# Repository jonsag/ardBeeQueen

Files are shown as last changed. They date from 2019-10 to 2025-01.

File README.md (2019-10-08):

# ardBeeQueen
A simple project to control a bee queen breeding chamber

Parts needed
===============
1 x Arduino Pro Mini, kjell.com art#87964  
1 x Arduino USB to Serial Converter, kjell.com art#87872  
2 x Arduino Single Relay Module, kjell.com art#87878  
1 x LCD Display, kjell.com art#90215  
1 x Dallas 1-wire Temp and Humidity Sensor DHT11, kjell.com art#87877 or  
1 x Dallas 1-wire Temp and Humidity Sensor DHT22, kjell.com art#90647  
1 x Rotary encoder, kjell.com art#87918  
1 x 10kohm Potentiometer, kjell.com art#90633  
1 x 220ohm resistor  
1 x 10K ohm resistor  
2 x 0,47uF capacitor  

Casing to hold everything

Wires and soldering material  

If you want to build a PCB using the Gerber file you will also need some headers and connnectors.  

Building electrical  
===============
Use schemes ardBeeQueenFritz* or Schematic_ardBeeQueen-v2_ardBeeQueen-v2_* to build.  
If you do not use the encoder you must still pull up D7 with a 10K resistor to VCC.  

Eagle PCB  
===============
If using the 50x52 PCB in Documents/Eagle directory, you can mount it in box electrokit.com, art#12109003  
Outside measures: 69 x 102 x 37 mm  
Inside measures: 63 x 96 x 33 mm  

If using the 105x84 PCB in Documents/Eagle directory, you can mount it in box electrokit.com, art#12109005  
Outside measures: 103 x 148 x 56 mm  
Insode measures: 96 x 142 x 52 mm  

Note
===============
All commands in the following instructions are run on Linux  
All links are valid and versions are the latest as of february 2019  

Set up Arduino IDE
===============
Go to https://www.arduino.cc/en/main/software and download Arduino IDE for your architecture and system  
>$ wget https://downloads.arduino.cc/arduino-1.8.10-linux64.tar.xz  
>$ tar xvJf arduino-1.8.10-linux64.tar.xz -C ~/bin/  
>$ ln -s arduino-1.8.10/arduino ~/bin/arduino  

Get libraries 
---------------

Adafruit Unified Sensor library  
---------------
Download library from https://www.arduinolibraries.info/libraries/adafruit-unified-sensor  
>$ wget http://downloads.arduino.cc/libraries/github.com/adafruit/Adafruit_Unified_Sensor-1.0.3.zip  
>$ unzip Adafruit_Unified_Sensor-1.0.3.zip -d ~/bin/arduino-1.8.10/libraries/  
>$ mv ~/bin/arduino-1.8.10/libraries/Adafruit_Unified_Sensor-1.0.3 ~/bin/arduino-1.8.10/libraries/Adafruit_Unified_Sensor  

DHT sensor library  
---------------
Download library from https://www.arduinolibraries.info/libraries/dht-sensor-library  
>$ wget http://downloads.arduino.cc/libraries/github.com/adafruit/DHT_sensor_library-1.3.7.zip  
>$ unzip DHT_sensor_library-1.3.7.zip -d ~/bin/arduino-1.8.10/libraries/  
>$ mv ~/bin/arduino-1.8.10/libraries/DHT_sensor_library-1.3.7 ~/bin/arduino-1.8.10/libraries/DHT_sensor_library  

Programming the Arduino Mini Pro
===============

If using the Arduino USB 2 Serial  
--------------------
Connect the programmer to your Pro Mini  
GND/BLK -> GND  
+5V -> VCC  
TX -> RX  
RX -> TX  
EXT RESET -> GRN

Open your sketch in Arduino IDE  
Select 'Tools'->'Port'  
* /dev/ttyACM0 or  
* /dev/ttyUSB0  

Select 'Tools'->'Board'  
For the 3.3V versions of the Arduino Pro Mini, select:  
* Arduino Pro or  
* Pro Mini (3.3V, 8 MHz) w/ ATmega328P or  
* Arduino Pro or  
* Pro Mini (3.3V, 8 MHz) w/ ATmega168  
(depending on the microcontroller on your board)  
For the 5V versions of the Arduino Pro Mini, select  
* Arduino Duemilanove or  
* Nano w/ ATmega328P or  
* Arduino Diecimila, Duemilanove (this is what I used) or  
* Nano w/ ATmega168

If using the PC-PL2303 Cable  
---------------
Black cable -> GND  
Green cable -> TXD  
White cable -> RXD  
Red cable -> VCC (5V)  

You will have to press the reset button on the arduino to reset it right before the upload from Arduino IDE.  

Fritzing  
===============
Download fritzing at http://fritzing.org/download/  

>$ wget http://fritzing.org/download/0.9.3b/linux-64bit/fritzing-0.9.3b.linux.AMD64.tar.bz2  
>$ tar jxvf ~/Downloads/fritzing-0.9.3b.linux.AMD64.tar.bz2 -C ~/bin/  
>$ ln -s fritzing-0.9.3b.linux.AMD64/Fritzing ~/bin/fritzing  

EasyEDA  
==============
Use easyEDA online at https://easyeda.com/editor or download client from https://easyeda.com/page/download  

>$ wget https://image.easyeda.com/files/easyeda-client-linux-x64.zip  
>$ unzip easyeda-client-linux-x64.zip  
>$ cd easyeda-client-linux-x64  
>$ sudo bash install.sh  

Download local router from https://docs.easyeda.com/en/PCB/Route/index.html#Local-Auto-Router  
>$ wget https://image.easyeda.com/files/EasyEDA-Router-v0.8.1.zip  
>$ unzip EasyEDA-Router-v0.8.1.zip  
>$ cd EasyEDA-Router-v0.8.1  

Start router with  
>$ bash lin64.sh  

Autodesk EAGLE
===================
Download EAGLE at https://www.autodesk.com/products/eagle/free-download  

>$ tar xvzf Autodesk_EAGLE_9.3.1_English_Linux_64bit.tar.gz -C ~/bin  
>$ ln -s eagle-9.3.1/eagle ~/bin/eagle  

Start and sign in with your Autodesk account

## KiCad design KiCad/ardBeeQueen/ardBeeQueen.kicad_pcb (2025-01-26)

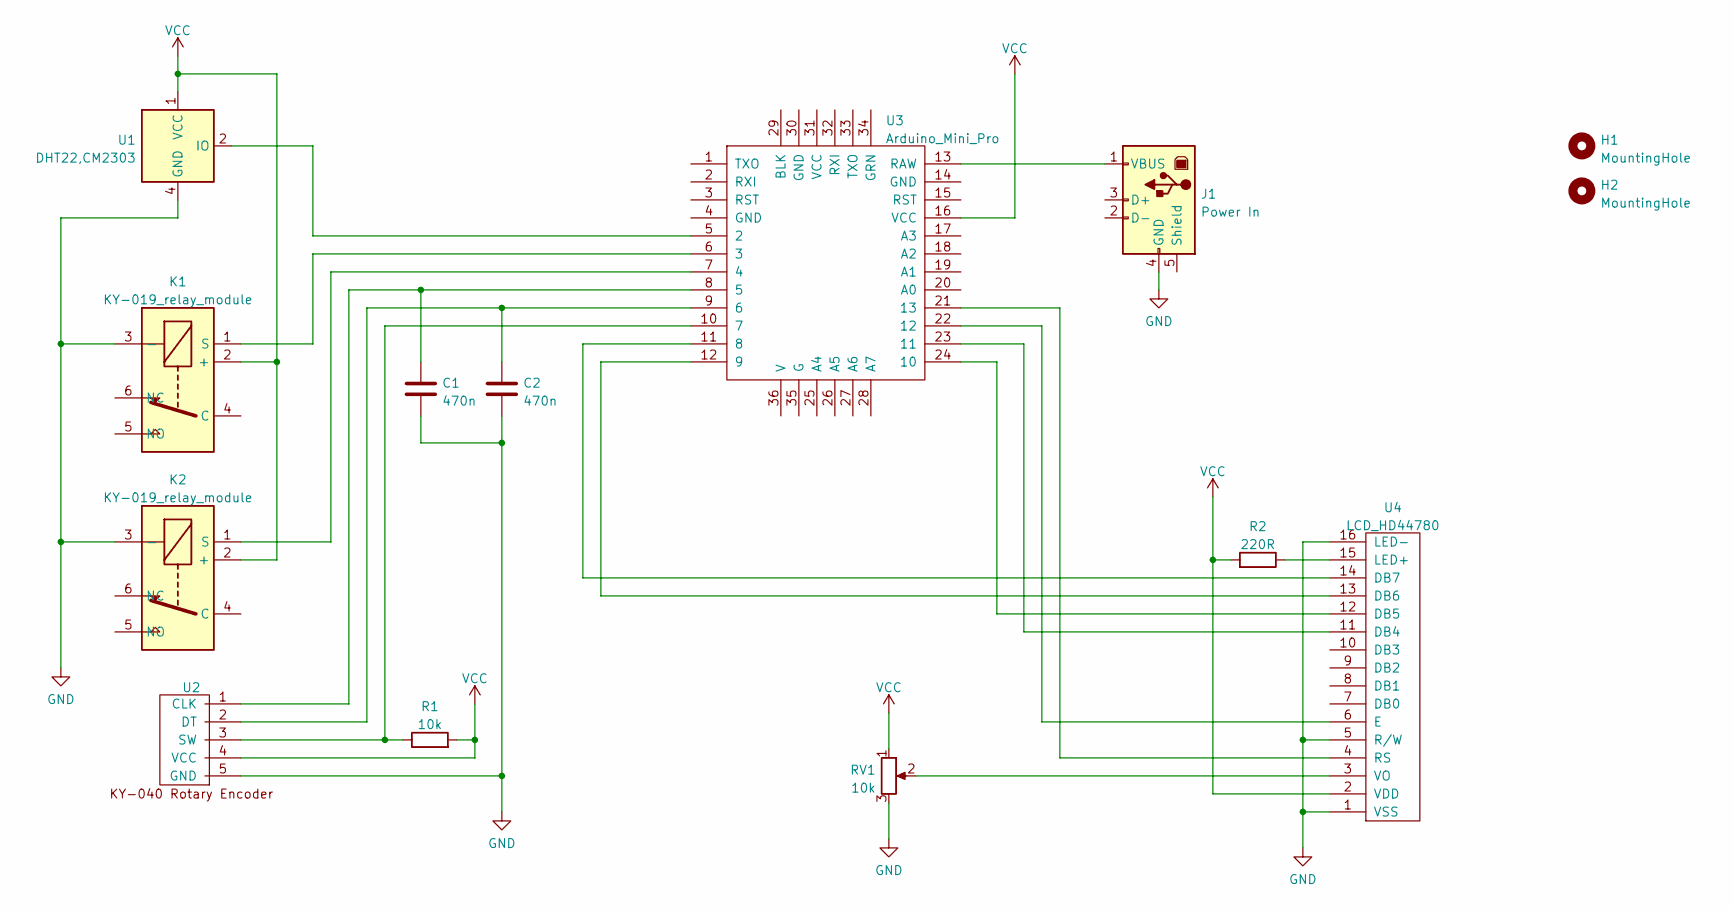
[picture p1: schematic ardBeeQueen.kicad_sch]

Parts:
C1, C2: 470n; C_Disc_D3.0mm_W1.6mm_P2.50mm_larg
H1, H2: MountingHole; MountingHole_3.2mm_M3
J1: Power In; USB_B_OST_USB-B1HSxx_Horizontal_large
K1, K2: KY-019_relay_module; 3-pin JST KY-019 relay
R1: 10k; R_Axial_DIN0207_L6.3mm_D2.5mm_P10.16mm_Horizontal_larger_pa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
R2: 220R; R_Axial_DIN0207_L6.3mm_D2.5mm_P10.16mm_Horizontal_larger_pa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
RV1: 10k; Potentiometer_Bourns_3339P_Vertical_large
U1: DHT22,CM2303; 3-pin JST DHT11, DHT22
U2: KY-040_Rotary_Encoder; 5-pin JST Rotary Encoder
U3: Arduino_Mini_Pro; Arduino_Pro_Mini_vC_only_sides_larger_pads
U4: LCD_HD44780; LCD_HD44780_16x2_w_headers_no outlinelarge

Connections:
GND: C1.2, C2.2, J1.4 (GND), K1.3 (-), K2.3 (-), RV1.3, U1.4 (GND), U2.5 (GND), U4.1 (VSS), U4.5 (R/W), U4.16 (LED-)
unnamed: C1.1, U2.1 (CLK), U3.8 (5)
unnamed: C2.1, U2.2 (DT), U3.9 (6)
unnamed: J1.1 (VBUS), U3.13 (RAW)
unnamed: K1.1 (S), U3.6 (3)
unnamed: K2.1 (S), U3.7 (4)
unnamed: R1.1, U2.3 (SW), U3.10 (7)
unnamed: R2.1, U4.15 (LED+)
unnamed: RV1.2, U4.3 (VO)
unnamed: U1.2 (IO), U3.5 (2)
unnamed: U3.11 (8), U4.14 (DB7)
unnamed: U3.12 (9), U4.13 (DB6)
unnamed: U3.21 (13), U4.4 (RS)
unnamed: U3.22 (12), U4.6 (E)
unnamed: U3.23 (11), U4.11 (DB4)
unnamed: U3.24 (10), U4.12 (DB5)
VCC: K1.2 (+), K2.2 (+), R1.2, R2.2, RV1.1, U1.1 (VCC), U2.4 (VCC), U3.16 (VCC), U4.2 (VDD)

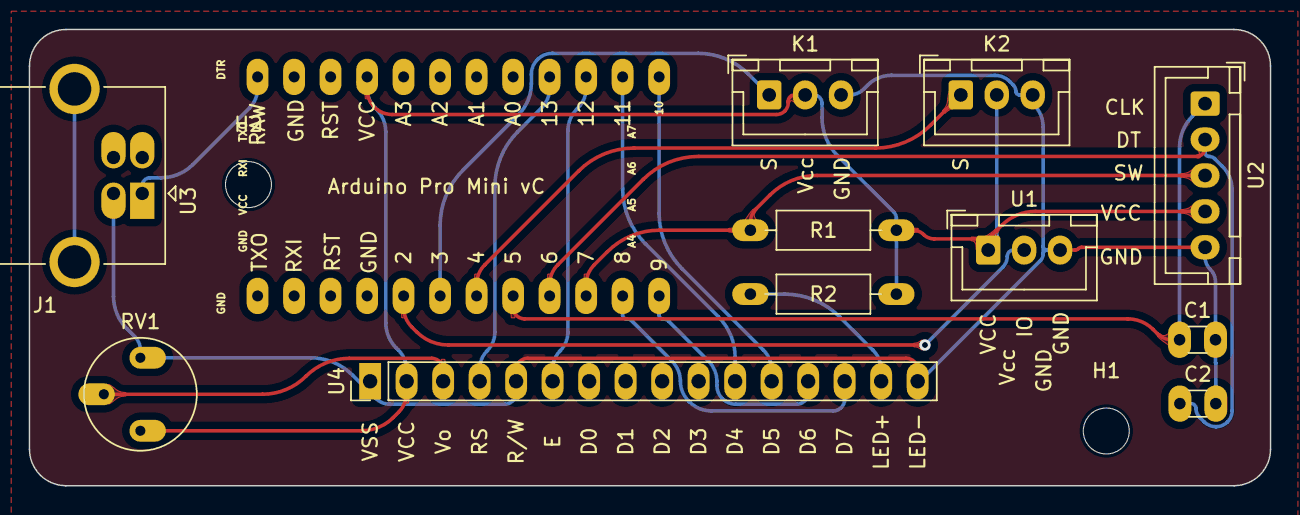
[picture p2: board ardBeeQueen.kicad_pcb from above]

Board: 2 copper layers, 86.4 x 31.7 mm, 14 parts (0 on the bottom side), 17 nets.

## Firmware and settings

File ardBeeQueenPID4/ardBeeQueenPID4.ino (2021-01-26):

String programName = "ardBeeQueenPID4";
String date = "201910020";
String author = "Jon Sagebrand";
String email = "jonsagebrand@gmail.com";

const bool plot = 1; // enable plotting function, all other output to serial will be suppressed

/*******************************
   EEPROM setup
 *******************************/
#include <EEPROM.h> // include EEPROM library
const int eeAddr = 0; // address to store the set point temp
double f; // stores the temp set in eeprom

/*******************************
   DHT setup
 *******************************/
#include <DHT.h> // include the DHT library
#define DHTPIN 2  // declare DHT pin number

// uncomment one of the below sensors
//#define DHTTYPE DHT11   // DHT 11 used
#define DHTTYPE DHT22   // DHT 22  (AM2302), AM2321
//#define DHTTYPE DHT21   // DHT 21 (AM230)

DHT dht(DHTPIN, DHTTYPE);  // initialize DHT sensor

unsigned long readMillis; // stores millis
const int waitTime = 2000; // millis to wait between reads

double hum = 0; // stores humidity
double temp = 0; // stores temperature
double dewPoint = 0; // calculated dew point
double dewPointFast = 0; // another calculated dew point
double hic = 0;

/*******************************
   Input/Output pins setup
 *******************************/
const int heatRelay = 3;  // heating relay
bool heatRelayState;
bool heatRelayStateLast = 0; // last state of operation

const int fanRelay = 4;  // cooling relay
bool fanRelayState = 0; // fan is always on/off
bool fanRelayStateLast = 0; // last state of operation

const int encoderCLK = 5; // rotary encoder CLK signal input pin
const int encoderDT = 6; // rotary encoder DT signal input pin
const int encoderSW = 7; // rotary encoders switch input pin, goes LOW when pressed

bool encoderCLKState = 0; // for storing encoder values
bool encoderDTState = 0;
bool encoderSWState = 0;
bool encoderDTStateLast = 0;
bool encoderSWStateLast = 0;

unsigned long encoderSWTimeMillis = 0; // the last time encoder button was toggled
const int debounce = 200;   // the debounce time, increase if the output flickers

/*******************************
   LCD setup
 *******************************/
#include <LiquidCrystal.h> // include the LCD library

// define LCD pins
const int LCD_RS = 13; // LCD RS, pin 4
const int LCD_EN = 12; // LCD E, pin 6, Enable
const int LCD_D4 = 11; // LCD D4, pin 11, databit 4
const int LCD_D5 = 10; // LCD D5, pin 12, databit 5
const int LCD_D6 = 9; // LCD D6, pin 13, databit 6
const int LCD_D7 = 8; // LCD D7, pin 14, databit7
/* other pins on LCD are:
   VSS, pin 1, GND
   VDD, pin 2, +5V
   V0, pin 3, 10k potentiometer, ends to +5V and GND, middle pin to V0, contrast
   R/W, pin 5, GND, Read/Write
   A, pin 15, 220ohm resistor, one end to +5V, other to A, back light anode, ~+4.2V
   K, pin 16, GND, back light cathode
   D0, pin 7, databit 0, not used/connected
   D1, pin 8, databit 1, not used/connected
   D2, pin 9, databit 2, not used/connected
   D3, pin 10, databit 3, not used/connected
*/

LiquidCrystal lcd(LCD_RS, LCD_EN, LCD_D4, LCD_D5, LCD_D6, LCD_D7); // initialize the LCD library

const int lcdColumns = 16; // columns and rows of the LCD
const int lcdRows = 2;

/*******************************
   PID setup
 *******************************/
#include <PID_v1.h> // include PID library by Brett Beauregard

double setPointTemp = 34.5; // the goal temp, in degrees celsius
double Output; // the PIDs output

/* PID tuning with the Ziegler-Nichols method
 *  Kp0 = The amplification when self oscillation occurs
 *  T0  = The period time of the oscillation
 *        P         PI        PID
 *   Kp   Kp0*0,5   Kp0*0,45  Kp0*0,6
 *   Ti   Off       T0/1,2    T0/2
 *   Td   Off       Off       T0/8
*/
//double Kp = 1, Ki = 2500.0, Kd = 625.0; // specify PID tuning variables
//double Kp = 1, Ki = 1.0, Kd = 1.0; // specify PID tuning variables
double Kp = 0.1, Ki = 5000.0, Kd = 1375.0; // specify PID tuning variables
PID myPID(&temp, &Output, &setPointTemp, Kp, Ki, Kd, DIRECT);

const unsigned long windowSize = 30000; // the time which the PID distributes between ON and OFF
bool PIDCalculated; // for checking if PID has been calculated
unsigned long windowTime;
unsigned long onTimeVal; // on time value

/*******************************
   Text output setup
 *******************************/
String valString = ""; // for calculation of length of values
int valLength;

String setPointTempText = "SP:"; // text to print before values on LCD
String actualTempText = "A:";
String humidityText = "Hm:";

const int setPointYOffset = 0; // LCD text offsets
const int actualTempYOffset = 9;
const int humidityYOffset = 0;
const int PIDYOffset = 8;

char dtostrfbuffer[5]; // buffer to store float to string

void setup(void) {
  /*******************************
    start LCD
  *******************************/
  lcd.begin(lcdColumns, lcdRows); // start LCD

  lcd.setCursor(0, 0); // print a message to the LCD
  lcd.print(programName);
  lcd.setCursor(0, 1);
  lcd.print("Booting ...");

  /*******************************
    start serial
  *******************************/
  lcd.setCursor(0, 1);
  lcd.print("Starting serial ...");
  Serial.begin(9600); // start serial port

  if (!plot) {
    Serial.println(programName); // print information
    Serial.println(date);
    Serial.print("by ");
    Serial.print(author);
    Serial.println(email);
    Serial.println();
  }

  /*******************************
    read value from eeprom
  *******************************/
  if (!plot) {
    Serial.println("Reading last temp from eeprom ...");
  }
  lcd.setCursor(0, 1);
  lcd.print("Reading last temp ...");
  f = 0.00f;
  EEPROM.get(eeAddr, f); // read set point from eeprom
  if (!plot) {
    Serial.print("Found value: ");
    Serial.println(f);
    Serial.println();
  }

  if (isnan(f)) { // check if there is a value stored in eeprom
    if (!plot) {
      Serial.println("No value found in eeprom");
      Serial.print("Storing value: ");
      Serial.println(setPointTemp);
      Serial.println();
    }
    EEPROM.put(eeAddr, setPointTemp); // if not, store the predefined val
  } else {
    if (!plot) {
      Serial.print("Found setpoint stored in eeprom: ");
      Serial.println(f);
      Serial.println("Using it as set point temperature");
      Serial.println();
    }
    setPointTemp = f; // else use it as set point
  }

  /*******************************
    start DHT
  *******************************/
  if (!plot) {
    Serial.println("Starting DHT sensor ...");
    Serial.println();
  }
  lcd.setCursor(0, 1);
  lcd.print("Starting sensor ...");
  dht.begin();  // start up dht sensors

  /*******************************
    define in- and outputs
  *******************************/
  if (!plot) {
    Serial.println("Starting outputs  ...");
  }
  lcd.setCursor(0, 1);
  lcd.print("Starting outputs ...");
  pinMode(heatRelay, OUTPUT);
  pinMode(fanRelay, OUTPUT);

  // rotary encoder pins
  if (!plot) {
    Serial.println("Starting inputs ...");
    Serial.println();
  }
  lcd.setCursor(0, 1);
  lcd.print("Starting inputs ...");
  pinMode(encoderCLK, INPUT);
  pinMode(encoderDT, INPUT);
  pinMode(encoderSW, INPUT);

  /*******************************
    start PID
  *******************************/
  if (!plot) {
    Serial.println("Starting PID ...");
    Serial.println();
  }
  lcd.setCursor(0, 1);
  lcd.print("Starting PID ...");
  myPID.SetOutputLimits(0, 1000); // 1000 steps in the control loop
  myPID.SetSampleTime(1000); //default is 100 miliseconds
  myPID.SetMode(MANUAL);// clears windup anc verifies PID calculations are correct based on sample time
  delay(5000); // prep the millis() timer below to have 5 seconds on it before PID starts calculating and turns on the heater
  myPID.SetMode(AUTOMATIC); // // start the PID ready for first calculation

  /*******************************
    start
  *******************************/
  lcd.clear();

  printSetPoint(); // print set point temp to LCD
  printHeatState(); // print heat state to LCD and serial
  printFanState(); // print fan state to LCD and serial

  if (!plot) {
    Serial.println("Program starts ...");
    Serial.println();
  }
}

void loop(void) {
  /*******************************
     Rotary Encoder
   *******************************/
  encoderCLKState = digitalRead(encoderCLK); // read rotary encoder
  encoderDTState = digitalRead(encoderDT);
  encoderSWState = digitalRead(encoderSW);

  if (!encoderSWState) { // button is pressed
    if (!encoderDTStateLast && encoderDTState) { // encoder has been turned
      if (!encoderCLKState) { // encoder is turned clockwise
        setPointTemp += 0.1;
        if (!plot) {
          Serial.print("Increasing set point. New value: ");
        }
      } else { // encoder is turned anti clockwise
        setPointTemp -= 0.1;
        if (!plot) {
          Serial.print("Decreasing set point. New value: ");
        }
      }
      if (!plot) {
        Serial.println(setPointTemp);
      }
    }
    encoderDTStateLast = encoderDTState; // store last value of encoder
  }

  if (encoderSWState != encoderSWStateLast) { // button has toggled
    if (!encoderSWState) { // button was pressed
      if (!plot) {
        Serial.println("Button is down");
      }
    } else { // button was released
      if (!plot) {
        Serial.println("Button is up");
        Serial.print("Storing new value to eeprom: ");
        Serial.print(setPointTemp);
        Serial.println(" ...");
      }
      EEPROM.put(eeAddr, setPointTemp); // write new set point to eeprom
    }
    encoderSWStateLast = encoderSWState; // store last value of encoder switch
    if (!plot) {
      Serial.println();
    }
  }

  printSetPoint(); // print the new set point temp to LCD

  /*******************************
     Temperature
   ********************************/
  if (encoderSWState) { // only read values if encoder button is UP
    if (millis() - readMillis >= waitTime) { // check if it's time to read sensor
      if (!plot) {
        Serial.println("Requesting humidity and temperature ...");
      }
      hum = dht.readHumidity(); // read humidity
      temp = dht.readTemperature(); // read temperature as celsius

      if (isnan(hum) || isnan(temp)) { // check if any reads failed
        if (!plot) {
          Serial.println(F("Failed to read from DHT sensor!"));
        }
        return;
      }
      else {
        if (plot) {
          Serial.print(setPointTemp); // print set point, temperature in celcius
          Serial.print(",");
          Serial.print(temp); // print process value, temperature in celsius
          Serial.print(",");
          Serial.print(hum); // prints humidity, relative %
          Serial.print(",");
          Serial.print(10 + Output / 100); // prints PID output 10-20
          Serial.print(",");
          Serial.println(heatRelayState * 10); // 0 = cooling off, 10 = heating, 20 = waiting
        }
      }
      printActualValues(); // print measured values to serial and LCD
      readMillis = millis(); // this is the time when sensor was last read
    }
  }

  /*******************************
     PID
   *******************************/
  PIDCalculated = myPID.Compute(); // this only calculates once every second and returns TRUE when it does
  writeToheatRelay(Output); // switch relay on or off
  if (PIDCalculated) {
    printPIDOutput(); // print PID output to LCD and serial
  }

  if (heatRelayState != heatRelayStateLast) { // there has been a change in heating or cooling
    printHeatState(); // print heat state to LCD and serial
    heatRelayStateLast = heatRelayState; // store last value
  }

  /*******************************
    Fan
  *******************************/
  digitalWrite(fanRelay, fanRelayState);

  if (fanRelayState != fanRelayStateLast) { // there has been a change in fan status
    printFanState(); // print fan status to LCD and serial
    fanRelayStateLast = fanRelayState; // store last value
  }
}

// dewPoint function NOAA
// reference: http://wahiduddin.net/calc/density_algorithms.htm
double dewPointFunction(double celsius, double humidity) {
  double A0 = 373.15 / (273.15 + celsius);
  double SUM = -7.90298 * (A0 - 1);
  SUM += 5.02808 * log10(A0);
  SUM += -1.3816e-7 * (pow(10, (11.344 * (1 - 1 / A0))) - 1);
  SUM += 8.1328e-3 * (pow(10, (-3.49149 * (A0 - 1))) - 1);
  SUM += log10(1013.246);
  double VP = pow(10, SUM - 3) * humidity;
  double T = log(VP / 0.61078);   // temp var
  return (241.88 * T) / (17.558 - T);
}

// delta max = 0.6544 wrt dewPoint()
// 5x faster than dewPoint()
// reference: http://en.wikipedia.org/wiki/Dew_point
double dewPointFastFunction(double celsius, double humidity) {
  double a = 17.271;
  double b = 237.7;
  double temp = (a * celsius) / (b + celsius) + log(humidity / 100);
  double Td = (b * temp) / (a - temp);
  return Td;
}

int intToStringToLength(int val) { // returns how many numbers in integer
  valString = String(val); // convert to string
  valLength = valString.length(); // count number of characters in string
  return valLength;
}

void printSetPoint() { // prints set point temp to LCD
  lcd.setCursor(setPointYOffset, 0);
  lcd.print(setPointTempText);
  valLength = setPointTempText.length(); // number of characters before digits
  lcd.setCursor(setPointYOffset + valLength, 0);
  lcd.print(setPointTemp, 1); // prints set point
  dtostrf(setPointTemp, 1, 1, dtostrfbuffer);
  valLength = valLength + strlen(dtostrfbuffer); // number of characters before digits + number of digits
  lcd.setCursor(setPointYOffset + valLength, 0);
  lcd.print((char)223); // prints degree sign
  lcd.setCursor(setPointYOffset + valLength + 1, 0);
  lcd.print(" ");
}

void printActualValues() { // prints measured values to serial and LCD
  dewPoint = dewPointFunction(temp, hum);   // calculate dew points in two different ways
  dewPointFast = dewPointFastFunction(temp, hum);
  hic = dht.computeHeatIndex(temp, hum, false);   // calculate heat index in Celsius (isFahrenheit = false)

  if (!plot) {
    Serial.print("    Temperature: ");
    Serial.println(temp);
    Serial.print("    Humidity: ");
    Serial.println(hum);
    Serial.print("    Dew Point: ");
    Serial.println(dewPoint);
    Serial.print("    Dew Point Fast: ");
    Serial.println(dewPointFast);
    Serial.print("    Heat Index: ");
    Serial.println(hic);
    Serial.println();
  }

  lcd.setCursor(actualTempYOffset, 0); // temp
  lcd.print(actualTempText);
  valLength = actualTempText.length();
  lcd.setCursor(actualTempYOffset + valLength, 0);
  lcd.print(temp, 1);
  dtostrf(temp, 1, 1, dtostrfbuffer);
  valLength = valLength + strlen(dtostrfbuffer);
  lcd.setCursor(actualTempYOffset + valLength, 0);
  lcd.print((char)223);
  lcd.setCursor(actualTempYOffset + valLength + 1, 0);
  lcd.print(" ");

  lcd.setCursor(humidityYOffset, 1); // humidity
  lcd.print(humidityText);
  valLength = humidityText.length(); // number of characters before digits
  lcd.setCursor(humidityYOffset + valLength, 1);
  lcd.print(hum, 0);
  dtostrf(hum, 1, 0, dtostrfbuffer);
  valLength = valLength + strlen(dtostrfbuffer);
  lcd.setCursor(humidityYOffset + valLength, 1);
  lcd.print("%  ");
}

void printPIDOutput() { // prints PID output to LCD and serial
  if (!plot) {
    Serial.print("SP: ");
    Serial.print(setPointTemp);
    Serial.print("°C, PV: ");
    Serial.print(temp);
    Serial.print("°C, PIDout: ");
    Serial.print(Output / 10);
    Serial.print("%, WT: ");
    Serial.print(windowTime);
    Serial.print(", OTV: ");
    Serial.println(onTimeVal);
    Serial.print(", HRS: ");
    Serial.println((heatRelayState) ? "On" : "OFF");
    Serial.println();
  }

  lcd.setCursor(PIDYOffset, 1);
  int output = round(Output / 10);
  lcd.print(output);
  valLength = intToStringToLength(output);
  lcd.setCursor(PIDYOffset + valLength, 1);
  lcd.print("%  ");
}

void printHeatState() { // prints heat state (ie C, H or W) to LCD and serial
  if (!heatRelayState) {
    if (!plot) {
      Serial.println("Cooling ...");
    }
    lcd.setCursor(15, 1);
    lcd.print("C");
  } else {
    if (!plot) {
      Serial.println("Heating ...");
    }
    lcd.setCursor(15, 1);
    lcd.print("H");
  }

  if (!plot) {
    Serial.println();
  }
}

void printFanState() { // prints fan state to LCD and serial
  if (fanRelayState) {
    if (!plot) {
      Serial.println("Fan ON");
    }
    lcd.setCursor(14, 1);
    lcd.print("F");
  } else {
    if (!plot) {
      Serial.println("Fan OFF");
    }
    lcd.setCursor(14, 1);
    lcd.print("x");
  }
  if (!plot) {
    Serial.println();
  }
}

void writeToheatRelay(double value) {
  windowTime = millis() % windowSize; // convert millis into a millisecond counter that resets at windowSize
  onTimeVal = (unsigned long)(value * (double)windowSize / 1000.0); // convert windowSize into seconds and multiply it by output which ranges from 0 to 1000

  if (onTimeVal > windowTime) {
    heatRelayState = 1;
  } else {
    heatRelayState = 0;
  }

  digitalWrite(heatRelay, heatRelayState); // set the output
  /*
    // short cycle prevention (Blink without delay)
    static unsigned long ShortCycleTimer;
    if ((millis() - ShortCycleTimer) >= (5000)) {
    if ((digitalRead(heatRelay) == LOW) && (heatRelayState = HIGH)) {
    	ShortCycleTimer = millis(); // this sets a blink without delay timer that prevents the following line from triggeringfor 5 seconds after it changes the output to HIGH
    }
    digitalWrite(heatRelay, heatRelayState); // set the output
    }
  */
}

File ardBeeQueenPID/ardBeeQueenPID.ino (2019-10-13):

// ardBeeQueenPID
/*
  The LCD circuit:
                               GND            display pin 1
    supply voltage for logic   +5V            display pin 2

   10K potentiometer:
   ends to +5V and ground
   LCD VO - contrast           wiper          display pin 3

   LCD RS pin                  digital pin 13 display pin 4
   LCD R/W pin                 GND            display pin 5
   LCD Enable pin              digital pin 12 display pin 6
   LCD D4                      digital pin 11 display pin 11
   LCD D5                      digital pin 10 display pin 12
   LCD D6                      digital pin 9  display pin 13
   LCD D7                      digital pin 8  display pin 14

   220ohm resistor to +5V
   back light anode:+4.2V      220ohm         display pin 15
   back light cathode          GND	          display pin 16
*/

// include EEPROM library
#include <EEPROM.h>
int eeAddr = 0; // address to store the set point temp

// include the DHT library
#include <DHT.h>
// define DHT pin
#define DHTPIN 2  // declare Pin Number
// uncomment one of the below sensors
//#define DHTTYPE DHT11   // DHT 11 used
#define DHTTYPE DHT22   // DHT 22  (AM2302), AM2321
//#define DHTTYPE DHT21   // DHT 21 (AM230)
// set up DHT sensor
DHT dht(DHTPIN, DHTTYPE);  // initialize DHT sensor
// wait time between temp reads, in milliseconds
unsigned long readMillis; // stores millis
int waitTime = 2000; // millis to wait between reads

// relay pins
const int heatingRelay = 3;  // relay heating
const int coolingRelay = 4;  // relay cooling
int heatState = 0; // current state of operation
int heatStateLast = 0; // last state of operation

// rotary encoder
// encoder pins
const int encoderCLK = 5; // rotary encoder CLK signal input pin
const int encoderDT = 6; // rotary encoder DT signal input pin
const int encoderSW = 7; // rotary encoders switch input pin, goes LOW when pressed
// for storing encoder values
int encoderCLKState = 0;
int encoderDTState = 0;
int encoderSWState = 0;
int encoderDTStateLast = 0;
int encoderSWStateLast = 0;
// times
unsigned long encoderSWTimeMillis = 0; // the last time encoder button was toggled
int debounce = 200;   // the debounce time, increase if the output flickers

// LCD
// include the LCD library
#include <LiquidCrystal.h>
// initialize the library with the numbers of the interface pins
LiquidCrystal lcd(13, 12, 11, 10, 9, 8);
// columns and rows of the LCD
int lcdColumns = 16;
int lcdRows = 2;

// Variables
float hum = 0; // read humidity
double temp = 0; // read temperature

// PID
// include PID library by Brett Beauregard
#include <PID_v1.h>
// define Variables we'll be connecting to
double setPointTemp = 34.5; // the goal temp, in degrees celsius
double Output; // the PIDs output
double gap; // the gap between setpoint and actual temp
// specify the links and initial tuning parameters
double aggKp=4, aggKi=0.2, aggKd=1; // aggressive PID parameters
double consKp=1, consKi=0.05, consKd=0.25; // conservative PID paramaters
PID myPID(&temp, &Output, &setPointTemp, consKp, consKi, consKd, DIRECT); // initiate PID with conservative parameters
//double Kp=2, Ki=5, Kd=1; // PID variables
//PID myPID(&temp, &Output, &setPointTemp, Kp, Ki, Kd, DIRECT);
// PID limits
int windowSize = 5000; // the time of the PID regulatory size(?)
unsigned long windowStartTime; // stores millis

double dewPoint = 0; // calculated dew point
double dewPointFast = 0; // another calculated dew point
float hic = 0;

// for calculation of length of values
String valString = "";
int valLength;

// text to print before temps
String setPointTempText = "SP:";
String actualTempText = "A:";

// buffer to store float to string
char dtostrfbuffer[5];

void setup(void) {

  // start LCD
  lcd.begin(lcdColumns, lcdRows);
  // print a message to the LCD
  lcd.setCursor(0, 0);
  lcd.print("ardBeeQueen");
  lcd.setCursor(0, 1);
  lcd.print("Booting ...");

  // start serial port
  lcd.setCursor(0, 1);
  lcd.print("Starting serial ...");
  Serial.begin(9600);

  Serial.println("ardBeeQueenPID");
  Serial.println("201910011");
  Serial.println("by Jon Sagebrand");
  Serial.println("jonsagebrand@gmail.com");
  Serial.println();

  // read set temp from eeprom
  Serial.println("Reading last temp from eeprom ...");
  lcd.setCursor(0, 1);
  lcd.print("Reading last temp ...");
  float f = 0.00f;
  EEPROM.get( eeAddr, f );
  Serial.println( f );

  // check if there is a value stored in eeprom
  // if so, then use it as set point,
  // else store the predefined value
  if ( isnan(f) ) {
    Serial.println("No value found in eeprom");
    Serial.print("Storing value: ");
    Serial.println(setPointTemp);
    EEPROM.put(eeAddr, setPointTemp);
  } else {
    Serial.print("Found a value stored in eeprom: ");
    Serial.println(f);
    Serial.println("Using it as set point temperature");
    setPointTemp = f;
    Serial.println();
  }

  // start DHT sensor
  Serial.println("Starting DHT sensor ...");
  lcd.setCursor(0, 1);
  lcd.print("Starting sensor ...");
  dht.begin();  // start up dht sensors

  // define in- and outputs
  // relay pins
  Serial.println("Starting outputs  ...");
  lcd.setCursor(0, 1);
  lcd.print("Starting outputs ...");
  pinMode(heatingRelay, OUTPUT);
  pinMode(coolingRelay, OUTPUT);
  // rotary encoder pins
  Serial.println("Starting inputs ...");
  lcd.setCursor(0, 1);
  lcd.print("Starting inputs ...");
  pinMode(encoderCLK, INPUT);
  pinMode(encoderDT, INPUT);
  pinMode(encoderSW, INPUT);

  // start PID
  Serial.println("Starting PID ...");
  lcd.setCursor(0, 1);
  lcd.print("Starting PID ...");
  myPID.SetOutputLimits(0, windowSize); // tell the PID to range between 0 and the full window size  
  myPID.SetMode(AUTOMATIC); // turn the PID on
  windowStartTime = millis();

  lcd.clear();

  printSetPoint();

  Serial.println("Program starts ...");
  Serial.println();

}
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

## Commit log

2018-05-15 Added fritz image
    [ardBeeQueenFritz.fzz]
2018-05-16 Now has a DHT11. Measures humidity abd temperature, has LCD, has both heating and cooling relay.
    [ardBeeQueenFritz.fzz]
2019-02-23 Updated fritz and sketch
    [ardBeeQueenFritz.fzz]
2019-02-24 Haf to add another sketch, as my Arduino Mini Pro is broken. D2 and D3 are shorted to each other, and D10 is not usable.
    [ardBeeQueenFritz.fzz]
2019-02-24 Added rotary encoder to sketch
    [ardBeeQueenFritz.fzz]
2019-02-25 Added rotary encoder for changing set point
    [ardBeeQueenFritz.fzz]
2019-02-25 Updated fritz with new components
    [ardBeeQueenFritz.fzz]
2019-02-26 Near completion- Also added schematics and PCB
    [ardBeeQueenFritz.fzz]
2019-03-05 Added board with mounted relays.# WARNING: head commit changed in the meantime
    delete
    [ardBeeQueenWMountHolesWMountedRelays105x84.brd, ardBeeQueenWMountHolesWMountedRelays105x84.sch]
2019-03-10 updated eagle docs
    [ardBeeQueen.brd, ardBeeQueen.sch, ardBeeQueenWMountHolesWMountedRelays105x84.brd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]
2019-10-11 added PID sketch
    [ardBeeQueenWMountHolesWMountedRelays105x84.brd]
2019-10-12 added another PID ino
2019-10-12 PID output to LCD
2019-10-12 added eagle schematics and PCBs
    [ardBeeQueen_12-pin_lcd 50x52.brd, ardBeeQueen_12-pin_lcd no holes.brd, ardBeeQueen_12-pin_lcd.sch]
2019-10-19 added air circulation fan
2019-10-20 deleted dew points and heat index from PIID3
2020-01-25 Eagle update
    [ardBeeQueen_12-pin_lcd.sch]
2021-01-26 schematic image
2022-05-29 moved to kicad
    [ardBeeQueen.brd, ardBeeQueen.kicad_pcb, ardBeeQueen.kicad_sch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]
2025-01-26 new kicad version
    [ardBeeQueen.kicad_pcb, ardBeeQueen.kicad_sch]
